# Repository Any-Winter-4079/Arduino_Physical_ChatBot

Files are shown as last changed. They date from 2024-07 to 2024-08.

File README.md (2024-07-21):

# Arduino Physical ChatBot

## Demo

## Description

[Missing description]

To run the project:

- `arduino/`: Arduino test and production sketches
- `esp32/`: ESP32 (-CAMs, -WROVER) test and production sketches
- `computer/`: Computer test and production scripts
- `requirements.txt`: Dependencies to install to run the robot

To help understand/use the project:

- `drawio/`: Drawio flowcharts to understand the inner workings of the robot
- `fritzing/`: Cable connections in Fritzing
- `guides/`: Step-by-step guides for the contruction of the robot
- `images/`: Images used in the guides
- `LICENSE`: Project license
- `README.md`: Overview of the project
- `.gitignore`: Files not pushed for being temporary or unnecessary

## Technical Overview

### Robot Components

Vision:

- 2x ESP32-CAM (with OV2640 camera and async web server) to send each eye's frame to the computer (upon request)

Audio:

- Input: KY-037 sound sensor (adjustable by potentiometer) triggers INMP441 I2S microphone for RECORDING_DURATION_MS (e.g., 5000 ms) audio recording. ESP32-WROVER sends this to computer via web sockets. Recording progress -e.g. Listening (3s)...- visualized on OLED SSD1306 I2C 128x64 screen.

- Output: Speaker with MAX98357A amplifier for audio playback. Audio (from Coqui.ai's text-to-speech conversion) sent from computer, received by ESP32-WROVER, and forwarded to MAX98357A.

Mobility:

- ESP32-WROVER server receives commands
- Arduino Uno forwards commands to:

  - L298N motor driver (for wheel movement)
  - 2x SG-90 servos (for up/down/left/right eye movement)

### Computer Components

Visual Processing:

- YOLOv8 (You Only Look Once) to detect objects - potentially obstacles (if both frames are available)
- SGBM (Semi-Global Block Matching) to estimate object depth (if both frames are available)
- DeepFace to recognize interlocutor's face (if at least 1 frame is available)

Audio Processing:

- Web sockets receive audio from ESP32-WROVER
- Whisper for speech-to-text transcription, discarding if below MIN_WORDS_THRESHOLD

Memory:

- ChromaDB to retrieve relevant long-term memories before every LLM or LMM call

AI Processing:

- LMM (Large Multimodal Model) to describe the view in a context-relevant way
- LLM (Large Language Model) to decide what to speak and which parts to move

## Guides with Diagrams

- [Connections](guides/00_connections.md)
- [Components](guides/01_components.md)
- [Chassis and motors](guides/02_chassis_and_motors.md)

## Setup

### Computer

Clone (and cd into) the repository:

```
git clone https://github.com/Any-Winter-4079/Arduino_Physical_ChatBot.git
cd Arduino_Physical_ChatBot
```

Create a virtual environment:

```
python -m venv venv
```

Activate the virtual environment:

- Windows: `venv\Scripts\activate`
- macOS/Linux: `source venv/bin/activate`

Install the dependencies:

```
pip install -r requirements.txt
```

### Robot

Install the Arduino IDE

Install esp32 by espressif into Boards Manager

Add:

- https://github.com/me-no-dev/AsyncTCP
- https://github.com/me-no-dev/ESPAsyncWebServer

into `XXXX/Arduino/libraries` (e.g. `Users/you/Documents/Arduino/libraries/` on macOS) for an async web server to send the images to your computer (to go from 1 fps to 37 fps at (320x240) resolution)

#### ESP32

To allow your ESP32s to communicate with your computer in your local network, replace:

```
const char* ssid1 = "****";
const char* password1 = "****";
IPAddress staticIP1(*, *, *, *);
IPAddress gateway1(*, *, *, *);
```

with your primary network (e.g. your home Wi-Fi) details

Replace:

```
const char* ssid2 = "****";
const char* password2 = "****";
IPAddress staticIP2(*, *, *, *);
IPAddress gateway2(*, *, *, *);
```

with your secondary (backup) network (e.g. phone hotspot)

And in the case of the ESP32-WROVER, replace:

```
const char* websocket_server_host1 = "*.*.*.*";
```

with your computer IP, when connected to your primary network

And:

```
const char* websocket_server_host2 = "*.*.*.*";
```

with your computer IP, when connected to your backup network

> **Note:** Make sure to provide unique IPs to each ESP32 (e.g. `192.168.1.180` and `192.168.1.181` for your ESP32-CAMs and `192.168.1.182` for your ESP32-WROVER, with your computer at `192.168.1.174`).

Then, for each of your 2 cameras (e.g. AiThinker, M5Stack Wide) and WROVER (e.g. Freenove), flash (through their USB type C or VCC/GND/TX/RX) `esp32/XXXX/production.ino` (e.g. `esp32/m5stackwide/production.ino`) with the following `Tools` setup:

```
Board: "ESP32 Dev Module"
Port: "/dev/cu.usbserial-110" (select your own)
CPU Frequency: "240MHz (WiFi/BT)"
Core Debug Level: "None"
Erase All Flash Before Sketch Upload: "Disabled"
Events Run On: "Core 1"
Flash Frequency: "80MHz"
Flash Mode: "QIO"
Flash Size: "4MB (32Mb)"
JTAG Adapter: "Disabled"
Arduino Runs On: "Core 1"
Partition Scheme: "Huge APP (3MB No OTA/1MB SPIFFS)"
PSRAM: "Enabled"
Upload Speed: "115200"
```

#### Arduino Uno

Flash (through its USB type B) `arduino/production.ino` with the RX pin temporarily disconnected

## Usage

## License

MIT

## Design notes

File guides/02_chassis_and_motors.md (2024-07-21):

For the creation of the robot, it is first suggested to collect the hardware components (Arduino Uno, L298N, INMP441, SG-90, MAX89357A, KY-037, breadboards, batteries, etc.), and propose a distribution on a potential chassis (considering aspects such as access for battery charging, flashing code to the Arduino Uno and ESP32s, etc.), to determine the number of levels -and the size of each level- necessary.

In this case, 2 levels (or floors) are created, using a wooden board or particle board of approximately 24x13x0.3cm for each level, and making use of a robot car template to draw the shape of the chassis to be cut (to leave space for the 2 or 4 wheels to connect to the motors -in this case, 2- and with 6 protrusions for the joining of the levels by hexagonal spacers). In Figures 1, 2, and 3, you can see the processes of sanding -after cutting-, drilling, and anchoring the motors.

The chassis, therefore, has two complete levels, joining components to the bottom of the first level, to the top of the first level, and to the top of the second level. Later, a third level is created partially, only at the back of the robot (similar to a spoiler), due to lack of space after the expansion (for audio and speech capabilities) compared to the initial idea of the robot, so it is suggested to increase the size of the chassis if a third level is to be avoided.

It is relevant to highlight that the motors are attached in this case to the bottom of the first floor, so that they are leveled with the free wheel (caster wheel) that is installed similarly below the first floor. Depending on the size of the free wheel, however, it may be necessary to install the motors on the top of the first floor, as the wheels attached to the motors are usually significantly larger than the free wheel, and it is important to keep the lower chassis leveled.

The result of this first phase of construction can be seen in Figure 4.

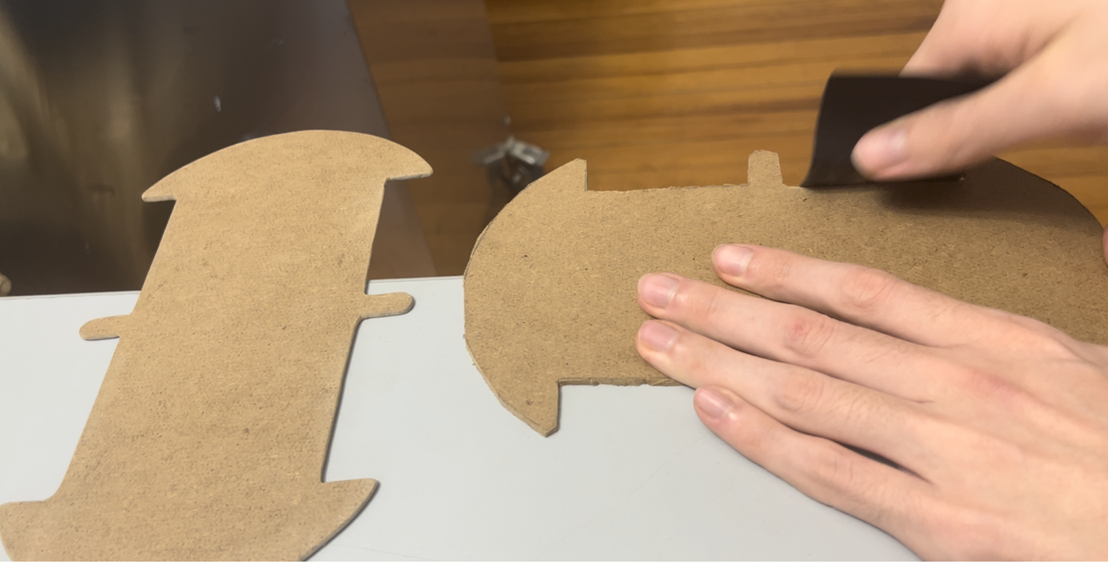
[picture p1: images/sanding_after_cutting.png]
sanding after cutting
<div align="center">
  <p>Figure 1. Sanding of the robot's chassis after cutting.</p>
</div>
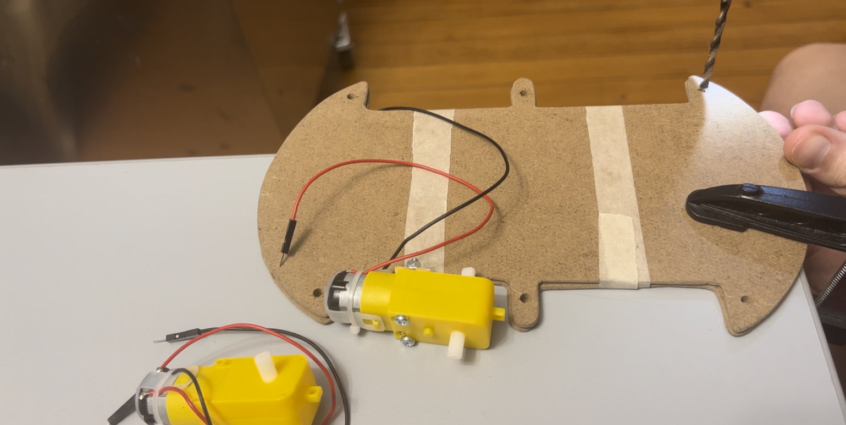
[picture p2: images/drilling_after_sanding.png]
drilling after sanding
<div align="center">
  <p>Figure 2. Drilling in both levels of the chassis for joining with hexagonal spacers after sanding.</p>
</div>
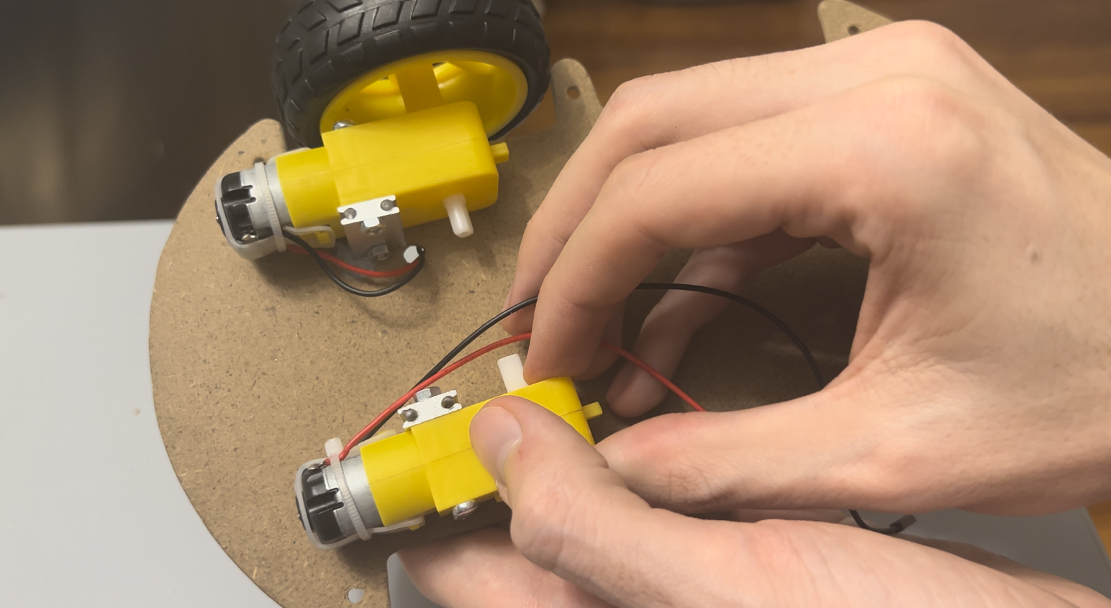
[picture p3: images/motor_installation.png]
motor installation
<div align="center">
  <p>Figure 3. Installation of motors on the lower part of the first level of the chassis.</p>
</div>
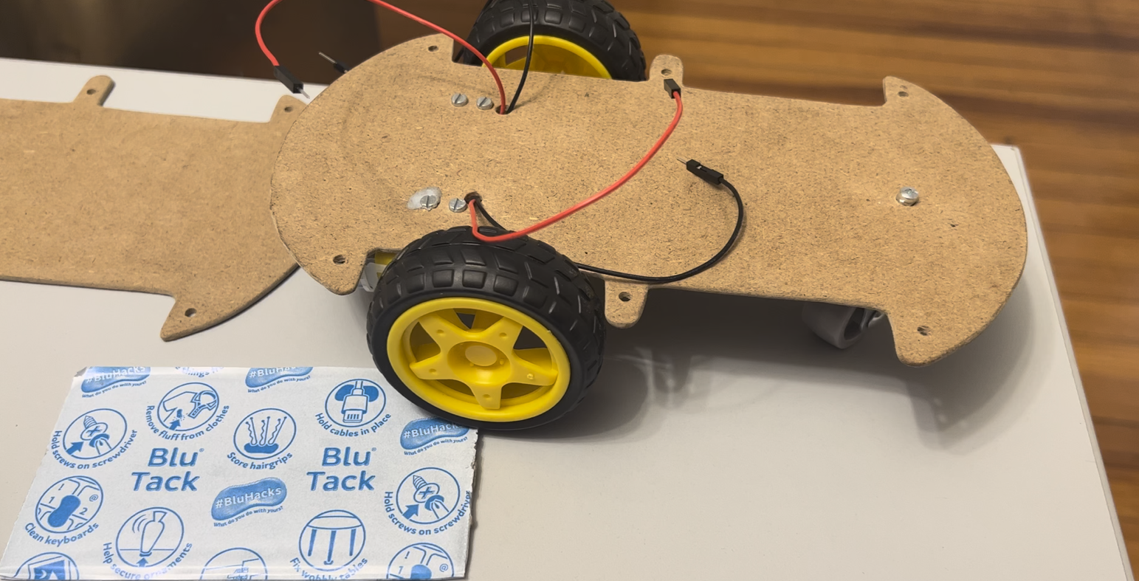
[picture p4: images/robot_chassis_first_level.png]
robot chassis first level
<div align="center">
<p>Figure 4. The first level of the chassis with two wheels connected to motors and a third free wheel.</p>
</div>

Regarding the purchase of the motor pack, note that either they are acquired with the +, - cables pre-soldered, or soldering will be required, as well as for their attachment to the chassis, it is recommended to acquire 2 motor mounts, to screw 2 screws horizontally - holding the motor to the mount - and 2 vertically - securing the mount to the chassis - in case they are not included in the pack.

After this first phase, it is recommended to test the hardware components (for example, connecting the Arduino Uno to the computer - by means of a USB A to USB B cable -, and uploading a basic program, such as Blink.ino), as well as their attachment to the top of the second level of the chassis - using the default M3 holes. A snapshot of this process can be seen in Figure 5.

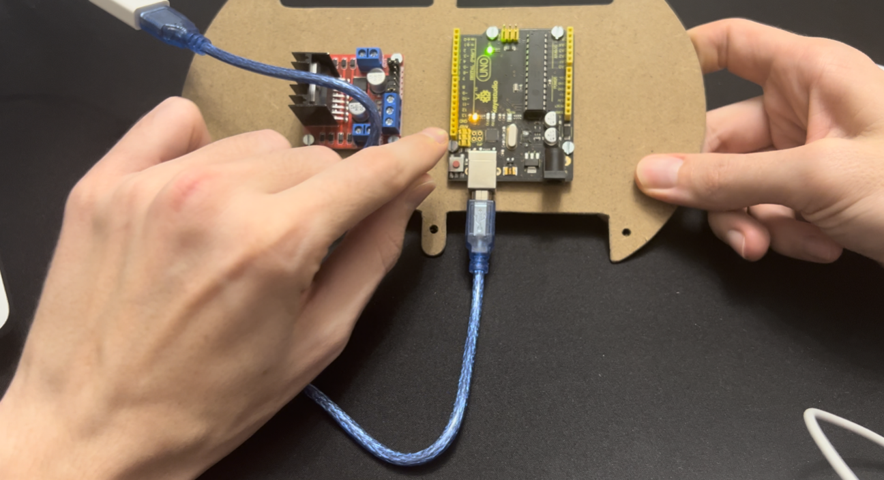
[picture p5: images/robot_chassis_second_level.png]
robot chassis second level
<div align="center">
  <p>Figure 5. Joining of Arduino Uno Rev3 and L298N to the top part of the second level of the chassis by M3 screws and connection of Uno to computer for uploading of the Blink.ino sketch.</p>
</div>

After testing the first components, it is suggested to install a battery - preferably rechargeable - and a breadboard to the top of the lower level of the chassis. In this case, Blue Tack is used for joining, to allow easy disassembly if necessary. It is important here that the battery charging connector (such as micro-USB B), and the breadboard pins are easily accessible, to facilitate charging tasks and connection of components to the power columns (+, -).

After this, both levels of the chassis can be joined with hexagonal spacers and M3 cap screws - although, if a third level is needed, headless M3 screws would be required for joining to the second level, so that both ends can be screwed into a hexagonal spacer.

Once both parts of the chassis are joined, it is suggested to connect the + and - cables of the motors to OUT1, OUT2 (right motor, from the robot's perspective) and OUT3, OUT4 (left motor) of the L298N, and power all components, connecting +, - of the 7.4V battery to one of the breadboard's power columns (+, -), where we connect our L298N and Arduino Uno. In the case of the L298N, note that, since the battery provides 7.4V, the +12V and GND input are used, while in the case of the Uno Rev3, the DC barrel jack is used, as using the 5V or 3.3V input would damage our component. For all connections, Dupont cables are used.

At this point, if desired, the operation of the motors can be tested (see: [move_motors](../arduino/test/move_motors.ino)) by connecting pins 8 and 7 of the Arduino Uno to IN1 and IN2 of the L298N (to control the direction of rotation, forward, backward or stop, of the right wheel) and pins 5 and 4 to IN3 and IN4 (to control the direction of rotation of the left wheel). Additionally, by connecting pins 6 and 3 (for pulse-width modulation) of the Arduino Uno to ENA and ENB of the L298N, values from 0 to 255 can be written (on these pins 6 and 3 of the Arduino Uno), which the L298N will interpret in ENA and ENB as indicators of the speed at which the right and left motors should move, respectively, according to the duration of the pulses. This idea of PWM (pulse-width modulation), where information is not only sent by modifying the voltage (usually, 5V or 0V) but also the duration of the pulses (which ultimately modifies the average voltage), can be observed in Figure 6.

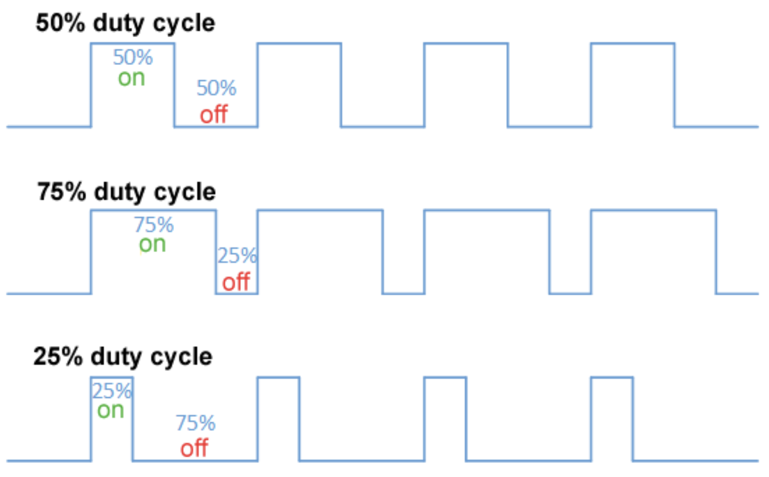
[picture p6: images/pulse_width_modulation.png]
pulse-width modulation
<div align="center">
  <p>Figure 6. Pulse-width modulation. By <a href='https://commons.wikimedia.org/w/index.php?curid=72876123'>Thewrightstuff - Own work, CC BY-SA 4.0</a></p>
</div>

The result of the joining of both levels can be observed in Figure 7. Note that there is an additional connection to GND and 5V of the L298N (initially intended to power a camera) that can be ignored. Moreover, it is recommended to lubricate the free wheel if it does not spin easily, and ensure it aligns with the direction of movement of the robot.

<div align="center">
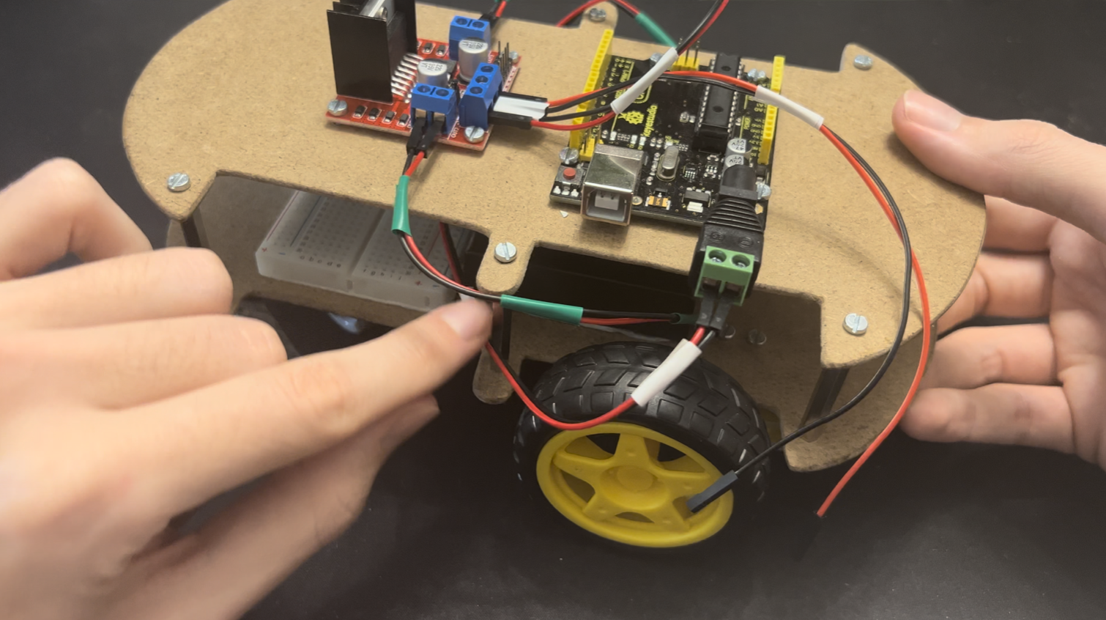
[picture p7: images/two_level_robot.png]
two level robot
  
  <p>Figure 7. 2-level view with Arduino Uno Rev3 and L298N on the upper level and 7.4V battery, 400-pin breadboard, wheels, and motors on the lower level.</p>
</div>

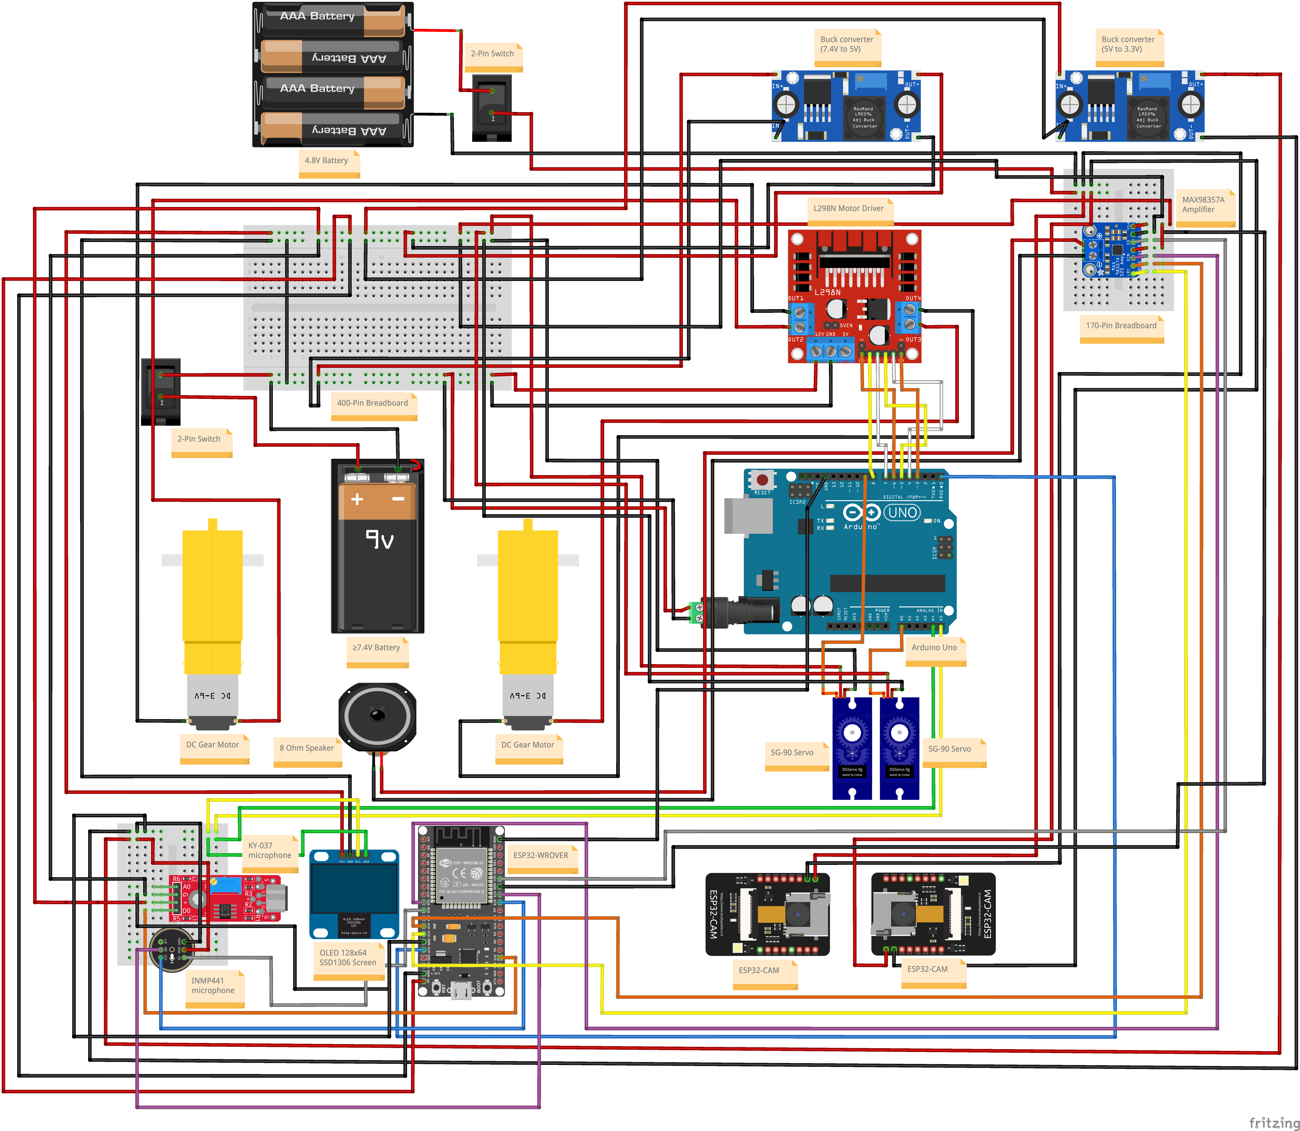
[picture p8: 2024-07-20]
images/connections.png

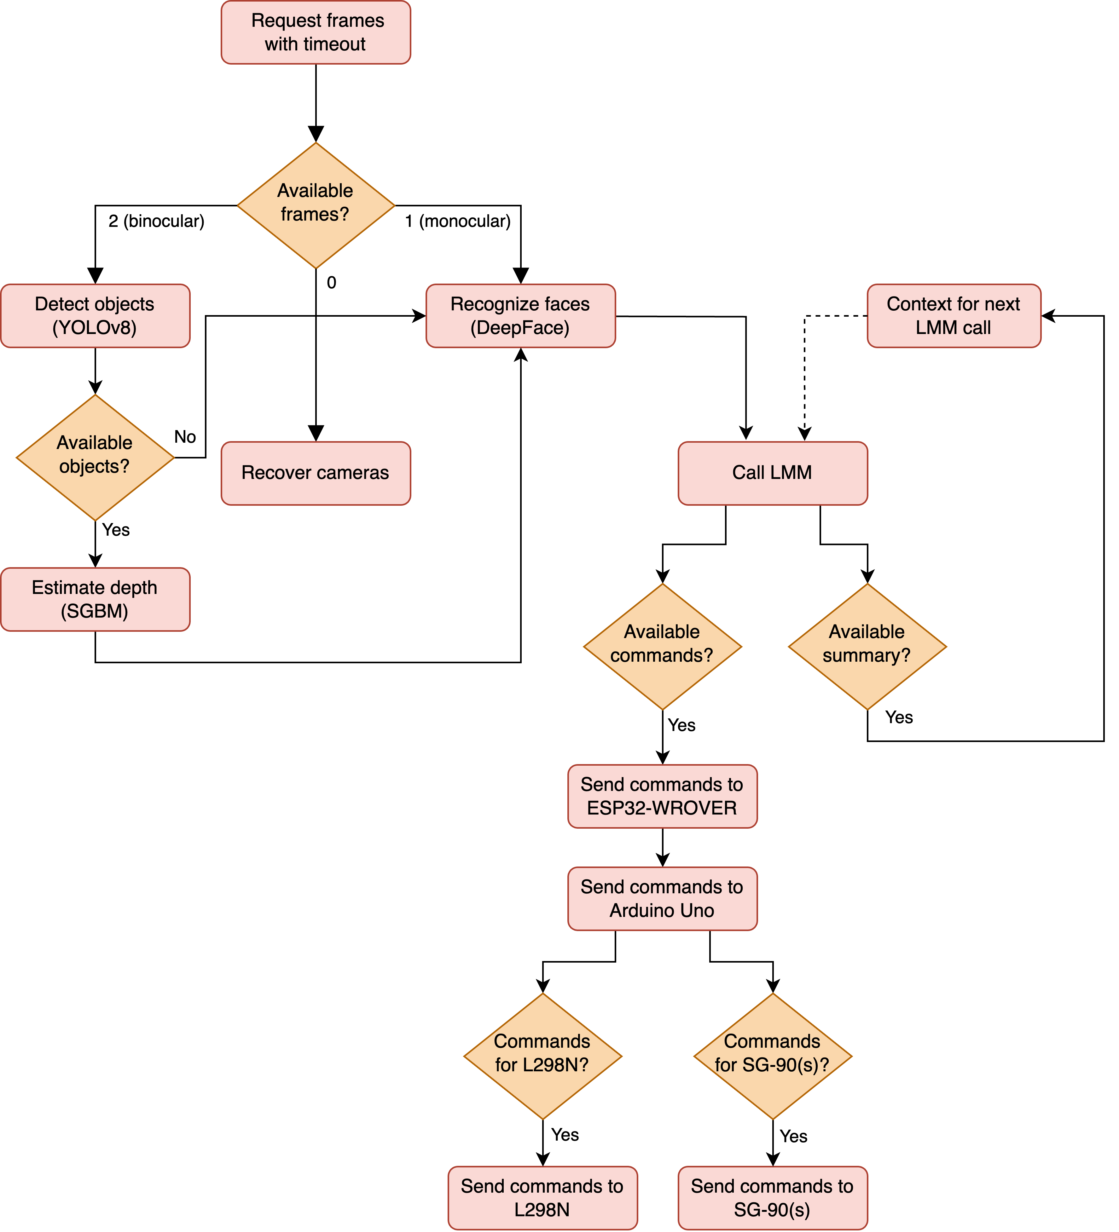
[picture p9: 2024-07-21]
images/driving_without_RAG.png

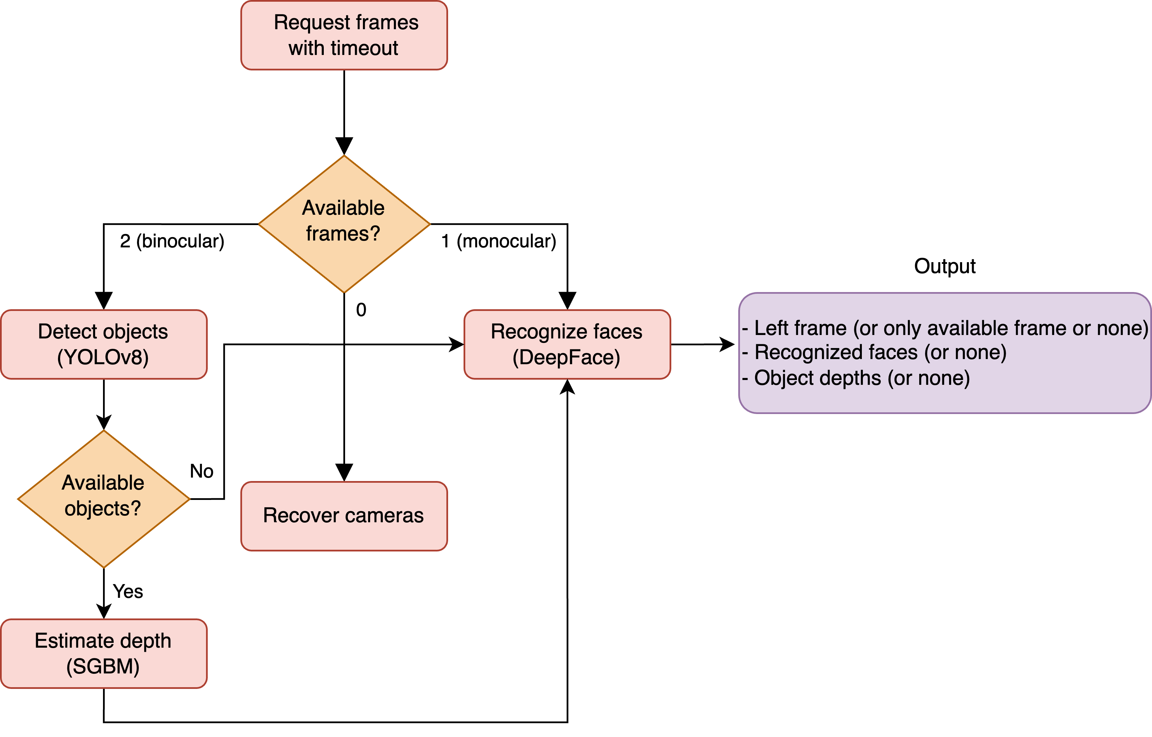
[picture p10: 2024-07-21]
images/vision_preprocessing.png

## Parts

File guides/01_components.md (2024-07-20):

The full list of components, available at both Amazon and AliExpress, is:

- 1x 7.4V rechargeable battery - in this case, micro-USB B type.
- 4x 1.2V rechargeable AA batteries (with holder and switch).
- 2x voltage reducers (buck converters) - adjustable by potentiometer.
- 1x 2-pin switch - and another switch if one is not available in the battery holder.
- 1x 400-pin breadboard.
- 2x 170-pin breadboards.
- Dupont male-to-male, male-to-female, female-to-female cables.
- 1x Arduino Uno Rev3.
- 1x DC barrel jack (DC power jack) - to power the Uno Rev3.
- 1x L298N motor driver.
- 2x SG-90 servos - to move the eyes horizontally and vertically.
- 2x ESP32-CAM - in this case, Ai-Thinker and M5Stack Wide, though both can be of the same model.
- 1x ESP32-WROVER (or ESP32-CAM without using the camera) - in this case, 1x Freenove ESP32-WROVER CAM Board.
- 2x OV2640 with 160-degree fisheye lenses.
- 1x 128x64 OLED SSD1306 I2C display.
- 1x KY-037 sound detection microphone.
- 1x INMP441 I2S microphone - for voice capture.
- 1x MAX98357A I2S amplifier.
- 1x 3W and 8Ω speaker.
- 2x 3-6V DC motors with gearbox - ending in copper, Dupont, or male JST.
- 2x DC Motor mounts, if the motors do not include them - to screw with 2 horizontal screws and 2 vertical screws each motor to the chassis.
- 2x Female JST to copper cables if the motors end in male JST.

Additionally, the following materials are necessary or recommended for the construction of the chassis, as well as securing components, and the construction of the eyes:

- 2x Wheels - 1x for each gearbox motor.
- 1x Free wheel of 3cm Ø.
- 1x Wooden or particle board of ≥40x40x0.3cm.
- 1x Wooden board of ≥~11x4x0.8cm - for vertical movement of eyes.
- Hexagonal M3 spacers of ~4cm in length.
- M3 screws of ~1.5cm in length, with head and double thread (without head).
- M3 washers.
- Normal and self-locking M3 nuts.
- 2 M2 screws - for the OLED SSD1306 I2C.
- 2 M2 nuts - for the OLED SSD1306 I2C.
- Ping pong balls.
- 1x Epoxy Resin Kit.
- Paints and brushes.
- Red thread.
- Blue Tack.
- Colored adhesive tape.
- Super Glue-3 - or similar.

Similarly, although not part of the robot, the following tools and accessories are recommended:

- 1x Digital multimeter.
- 1x 24 TPI steel saw or similar.
- Sandpapers.
- 1x Drill Kit - for size M3.
- 1x Soldering Kit - for INMP441 and MAX98357A.
- Pliers - and, potentially, wire strippers.
- Screwdrivers.
- 1x Clamp - to hold during cutting.
- 1x Measuring tape.
- 1x Scissors.
- 1x Printer - and paper- to print the iris of the eyes and the calibration pattern for the ESP32-CAM.

And finally, for the software to work, the following tools and equipment are required:

- 1x Computer, to run the LLM.
- 1x Router for internet access and/or phone with hotspot.
- 1x USB-A to Serial converter (to flash the code to some ESP32-CAM models, such as Ai-Thinker) and/or USB-A to USB-C cable (to flash the code to other models, such as M5Stack Wide).
- 1x USB A to USB B cable - to flash the code to the Uno Rev3.
- 1x USB A to micro-USB B or similar cable - to charge the 7.4V battery.
- 1x AA battery charger, to recharge the camera batteries.

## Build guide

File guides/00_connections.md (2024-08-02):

The robot connections are shown in the diagram below.

It is strongly recommended to build and test the robot piece by piece (e.g. [02_chassis_and_motors](02_chassis_and_motors.md)) rather than assembling everything at once. This allows for easier troubleshooting and ensures each component is working correctly before continuing with the next part.

<div align="center">
  Connections
</div>

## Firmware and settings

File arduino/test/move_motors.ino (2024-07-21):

// Right motor (from the robot's perspective)
int INA = 6; // Control movement speed with pulse-width modulation: [0-255]
int IN1 = 8; // Control direction of movement: [0,1]
int IN2 = 7; // Control direction of movement: [0,1]

// Left motor
int ENB = 3; // Control movement speed with pulse-width modulation: [0-255]
int IN3 = 5; // Control direction of movement: [0,1]
int IN4 = 4; // Control direction of movement: [0,1]

// To control direction:
// 10 (right motor) 10 (left motor) -> Forward
// 01 (right motor) 01 (left motor) -> Backward
// 00 (right motor) 00 (left motor) -> Stop
// 01 (right motor) 10 (left motor) -> Rotate right
// 10 (right motor) 01 (left motor) -> Rotate left

// To control speed:
// Any value from 0 to 255. Due to friction and the weight of the robot,
// the min speed is set here to 135. Low speeds may not generate enough
// force to move the robot when it gets resistance from the ground.

// Make sure the caster wheel freely spins and aligns itself with
// the direction of motion when driving forward (or backward).
// If not, some lubrication may help.

int SHORT_WAIT_TIME = 500; // 0.5 seconds
int MEDIUM_WAIT_TIME = 1000; // 1 second
int LONG_WAIT_TIME = 3000; // 3 seconds

int TOP_SPEED = 255; // 100% duty cycle
int INTERMEDIATE_SPEED = 180; // 71% duty cycle
int LOW_SPEED = 135; // 53% duty cycle
int NO_SPEED = 0; // 0% duty cycle

void setup() {
    // Sets pins as output pins (meaning we'll write to them)
    pinMode(INA, OUTPUT);
    pinMode(IN1, OUTPUT);
    pinMode(IN2, OUTPUT);
    pinMode(ENB, OUTPUT);
    pinMode(IN3, OUTPUT);
    pinMode(IN4, OUTPUT);

    // Move forward (10 10)
    digitalWrite(IN1, HIGH);
    digitalWrite(IN2, LOW);
    analogWrite(INA, LOW_SPEED);

    digitalWrite(IN3, HIGH);
    digitalWrite(IN4, LOW);
    analogWrite(ENB, LOW_SPEED);

    delay(LONG_WAIT_TIME); // Wait (robot keeps moving)

    // Move backward (01 01)
    digitalWrite(IN1, LOW);
    digitalWrite(IN2, HIGH);
    analogWrite(INA, LOW_SPEED);

    digitalWrite(IN3, LOW);
    digitalWrite(IN4, HIGH);
    analogWrite(ENB, LOW_SPEED);

    delay(LONG_WAIT_TIME); // Wait (robot keeps moving)

    // Turn left (10 01)
    digitalWrite(IN1, HIGH);
    digitalWrite(IN2, LOW);
    analogWrite(INA, TOP_SPEED);

    digitalWrite(IN3, LOW);
    digitalWrite(IN4, HIGH);
    analogWrite(ENB, TOP_SPEED);

    delay(LONG_WAIT_TIME); // Wait (robot keeps moving)

    // Stop the motors
    digitalWrite(IN1, LOW);
    digitalWrite(IN2, LOW);
    digitalWrite(IN3, LOW);
    digitalWrite(IN4, LOW);

    delay(MEDIUM_WAIT_TIME); // Wait (robot stays still)

    // Turn right (01 10)
    digitalWrite(IN1, LOW);
    digitalWrite(IN2, HIGH);
    analogWrite(INA, TOP_SPEED);

    digitalWrite(IN3, HIGH);
    digitalWrite(IN4, LOW);
    analogWrite(ENB, TOP_SPEED);

    delay(LONG_WAIT_TIME); // Wait (robot keeps moving)

    // Stop the motors
    digitalWrite(IN1, LOW);
    digitalWrite(IN2, LOW);
    digitalWrite(IN3, LOW);
    digitalWrite(IN4, LOW);
}

void loop() {
    // Do nothing
}

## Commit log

2024-07-19 update readme with robot esp32 and arduino setup
2024-07-21 add chassis and motors guide, test sketch
2024-07-21 add fritzing connections
    [connections.fzz]
2024-08-01 update frizing/
    [connections.fzz]
